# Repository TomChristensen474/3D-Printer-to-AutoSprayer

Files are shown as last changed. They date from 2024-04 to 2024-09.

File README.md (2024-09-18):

# 3D-Printer-to-AutoSprayer
## Introduction
This project is aimed at creating an affordable, accessible autosprayer by modifying your 3D printer. The process is non-destructive and you will retain the existing functionality of your 3D printer.

Taking it from a boring 3D printer to 3D Printer + AutoSprayer:

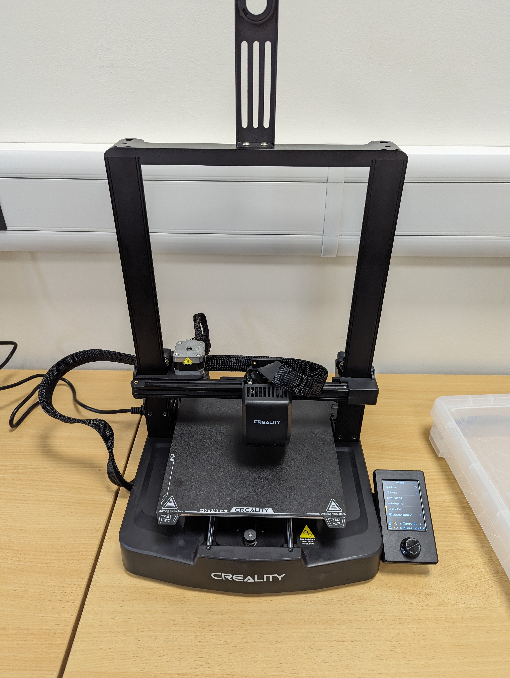
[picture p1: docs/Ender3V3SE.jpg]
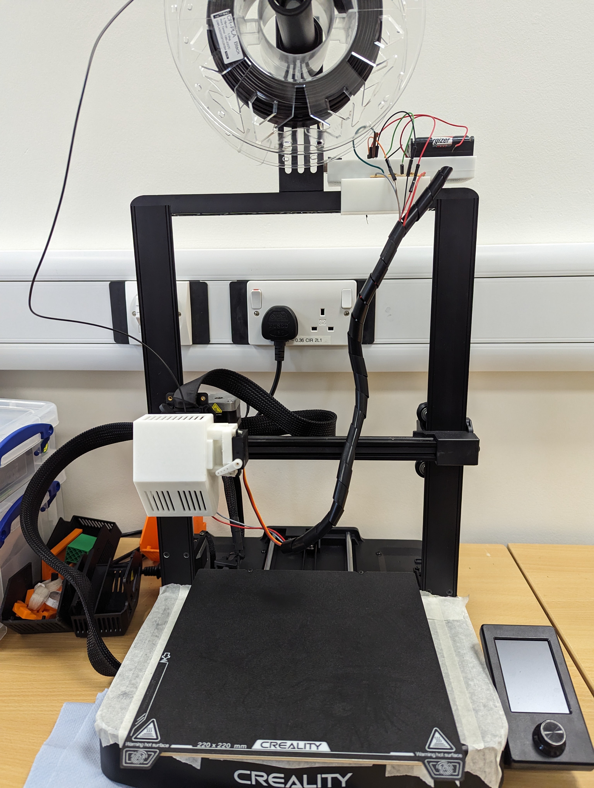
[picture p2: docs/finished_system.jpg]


https://github.com/user-attachments/assets/ce837ea1-1385-4ece-8191-b1b6b753dc1a

The video above shows a benchmark of the autosprayer's even spray-coating capabilities - apologies for Github's rotation of the portrait video.

This project was done using an Ender 3 V3 SE, the .stl files provided should therefore be adapted or replaced to suit your existing printer. But feel free to take inspiration from the designs. ;)

Speaking of inspiration: The idea for this project and some development was based off this original instructables article by user: Remi_Rafael so credit to them. <INSERT ORIGINAL INSTRUCTABLES>

## Quick-links
[System Requirements](#system-requirements)

[How does it work?](#how-does-it-work)

[How to set up](#how-to-set-up)

[Quick code breakdown](#the-code---what-does-it-do)

## System requirements
#### Expensive purchases :( 
* 3D printer
* Airbrush
* Compressor for airbrush
* Inks/Paints for airbrushing

#### Equipment you may already have on hand :)
* 2x Resistors in restistance ratio (<INSERT MY SPECIFIC ONES USED FOR ENDER 3 SYSTEM>)
* Arduino Uno (you can, of course, use whatever arduino you may have to hand, but the uno made it convenient with it's plethora of connections)
* 6xAA battery holder and (preferrably rechargeable) batteries (to power servo and circuit). If using an alternative method of powering the system, make sure it can handle the current draw of whatever servo you use. A simple USB will likely not be enough to power it.
* Servo motor (DS239-MG or equivalent) (<INSERT SPECIFIC ONE USED / SPECS>) 
* Heat-set threaded inserts and screws
* Cables
* Cable wrap for cable management

## How does it work?
#### Step 1 - Mounting the Airbrush
The airbrush is mounted onto the existing print-head using custom 3D printed models. To mount to the Ender 3 VS SE I used for the project, I chose to model a replacement print-head with a mount for the airbrush on the side. The .stl files for this printer are included.

#### Step 2 - Controlling Movement of the Print-Head/Airbrush
G-code is a widely used set of instructions used to control CNC machines and 3D printers. We can take advantage of G-code's existing functionality to do things like move the print head (and therefore the airbrush) to the position we desire. The instructions we take advantage of in this system can be found in the GCODE_writer class.

#### Step 3 - Controlling When/Where/What we Spray
We can take advantage of the parts-cooling fan in the printer in order to send a signal to our system telling us when, where and how much we want our airbrush to spray. This is a specific G-code instruction and sets our fan speeds between a range of 0 and 255, sending a different amount of voltage to the pins of the fan. By 'hijacking' this voltage and reading it using our arduino, we can send a signal to our servo motor telling it to turn a lot or a little, pulling the airbrush trigger back more or less respectively.

The circuit used for this is displayed below - both in schematic-form and in a simulator for the less electrically-inclined like myself.

## How to set up
You've got all the hardware, and you're ready to get spraying. How do you set all this up? (If you're using a CNC gantry or alternative printer to the Ender 3 V3 SE, there may be some additional trial and error with modeling and printing your own mounting hardware).
### Step 1 - Printing the mounting hardware
.stl files for the mounting hardware can be found in the models folder of this repository. First let's print the airbrush mount. There are 3 models to connect the airbrush to the print-head: a replacement print-head cover, an extended trigger to allow your servo to pull back the airbrush trigger, and a 'mate' to this print-head cover to hold the airbrush in place.

The models directory also contains a clip to mount your circuit to the frame of the Ender 3 V3 SE. A separate model is included which screws into the clip to hold an arduino uno and a battery. If you are using alternative hardware to an Arduino Uno, you can remodel this whilst still being able to use the clip provided. (The screw holes provided are M3).

I recommend test fitting all components now.

### Step 2 - Set up your circuit
I have provided a circuit schematic and diagram in the [section here](#step-3---controlling-whenwherewhat-we-spray).
For a picture of my assembled circuit, see below. My machine was only a prototype, so I didn't make any effort to permanently fix components in place. For longer-term use I would definitely recommend putting some effort into making it fit more compactly and robustly together (perhaps converting the circuit design into a PCB to make it more compact also).

It's important to note for the circuit to work that all ground connections must be linked (printer fan [next section], battery(/power supply), Arduino).

### Step 3 - Connect your circuit to your printer
To connect your circuit to the printer, we solder two leads from our circuit to the voltage and ground connections on the fan that is attached to the print-head.

If you are using a CNC 3D gantry or simply don't want to solder a connection to the fan on your printer. You can still use a button-controlled circuit to tell the circuit when to spray manually and achieve great results.

### Run the code
Load the relevant Arduino sketch onto your Arduino depending on if you're automated or button controlled spraying. You can then disconnect it if you wish as your battery/power supply can power the Arduino.

To run the ```spray_an_area.py``` script to generate ```.gcode``` to spray a desired area. You can run ```src/gcode_generation/spray_an_area.py``` with the following flags to specify the area you want to spray

```--start-position x y``` - sets the start position to `x` and `y`

```--spray-area w h``` - sets the dimensions of area to be sprayed to `w` (width) and `h` (height) in mm

```--destination filename``` - sets the destination filename of the .gcode file e.g. 'spray_an_area' -> `spray_an_area.gcode`

```--layers n``` - repeat for `n` layers

```--no-temp``` - do not set a target temperature or wait for temperature stabilisation

(```static_GCODE_script.py``` is also included, it takes no arguments and may be useful for debugging.)

### Step 5 - Testing
Now that your circuit is all connected, let's give it a test before we finish the assembly. Your printer's control software should have some way of manually turning on and off the fans on the print head like this on the Ender 3 V3 SE's menu (control->temperature->fans) pictured below.

When the fans are switched on you should see (and hear) your servo actuating to its 'spray' position. When the fans are switched off, you should see it return to its 'resting' position.

If you are using manually controlled spraying, add a button to your circuit and test that your servo activates when a button is pressed.

### Step 6 - Assembly and dry run
Your servo will be attached to the airbrush mounting hardware and will therefore have wires dangling down from the printer's frame. To tidy up these wires along with the leads connecting to the printer's fan, I highly suggest getting some cable wrap to route them all together and prevent unecessary strain on individual cables.

You can now load your airbrush onto your mounting hardware (without any ink loaded in the paint cup), with the extended trigger. Mount the servo as well and position the servo arm primed to push back the airbrush trigger.

Run the gcode_generation script ```spray_an_area.py``` with your desired spray area position and size. Load this onto your printer's SD card (or used networked printing options) and hit print.

You should see your print head strafe over your specified spray area and your servo should pull back the airbrush trigger at the start and end of each strafe.

You can use this opportunity to hone in your spraying dimensions.

### Step 7 - Mask your printer to protect from stray paint
Wait, wait, wait before you start spraying! Make sure you mask off your print bed, and the area around it to prevent getting paint on it.

If your printer has a magnetic print bed like the Ender 3 V3 SE, I would recommned getting a second one so you can hot-swap between spraying and printing more easily.

### Step 8 - Get creating!
You can create stencils using a laser or vinyl cutter (or masking) and now generate consistently sprayed images.
You could adapt my spraying code to spray patterns or images directly without requiring a stencil.
You can spray functional inks like I've done in my demo below to quickly generate functional prototypes on 3D printed objects.

If you do end up creating anything using this repo I'd love to see so please get in touch and show off what you've done!

## The Code - what does it do?
It can be a little overwhelming for some to dive into a repo and try and decipher what all the code does without a little extra explanation so I thought I'd provide that here:

There are two main components to the code provided. In the ```gcode_generation``` folder you will find code for a simple script to spray an even coat across a specific area as this was my goal for the project. (I used my 3D modeling software to create a mask on top of my print in the pattern for the circuit I wanted to make using sprayed functional inks). However the ```GCODE_writer``` class is provided and can be adapted or modified to spray more complex patterns or images. The ```spray_an_area.py``` python script contains arguments that are listed in the [relevant section](#run-the-code).

In the ```arduino_sketches``` folder you will find two very similar scripts with the purpose of controlling the activation of a servo. ```automatic_spray.py``` is an example script that controls the spraying automatically from aforementioned G-code instructions for turning the fan on-and-off. ```button_spray.py``` is an alternative example where spraying can be manually controlled by button-press in the event that alternative printers do not provide as easy access to fan control as with the Ender 3 VS SE (I assume most will as print-heads must be cooled somehow).

Lastly (for my research purposes) there is an evaluation script (```evaluation.py```) provided. This was used for evaluating the performance of the system with regards to applying an even coat of acrylic paint across an paper by seeing how much light passed through - which is important for my application of spraying functional inks to create circuits. You can very likely ignore this but I thought I would include it nonetheless.

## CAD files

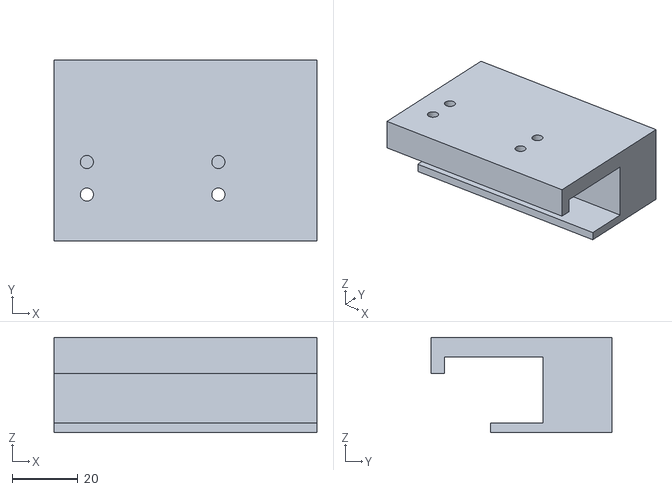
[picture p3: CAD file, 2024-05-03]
models/Ender_3_Clip v16.stl
80.0 x 55.0 x 29.0

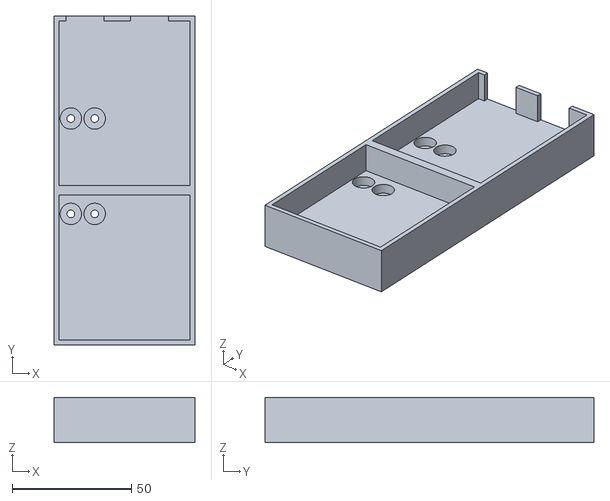
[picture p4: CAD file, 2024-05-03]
models/Ender_3_Uno_Mount v16.stl
59.0 x 138.0 x 19.0

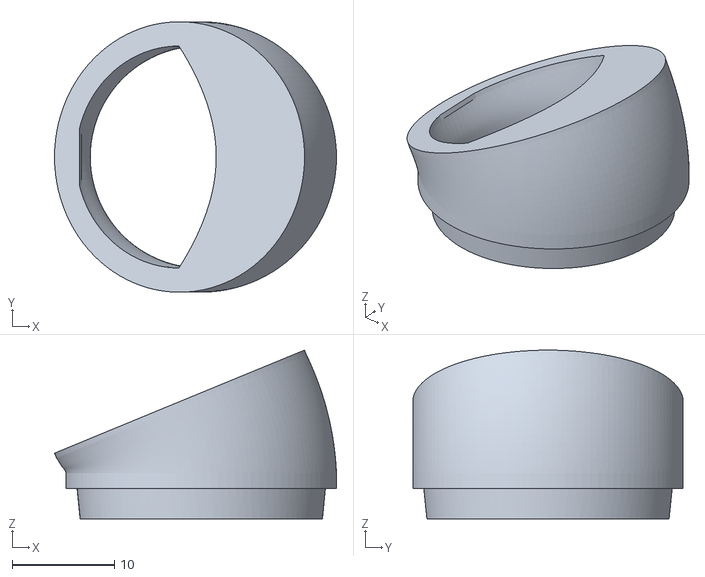
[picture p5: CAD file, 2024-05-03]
models/Airbrush cap v1.stl
27.6 x 26.5 x 16.5

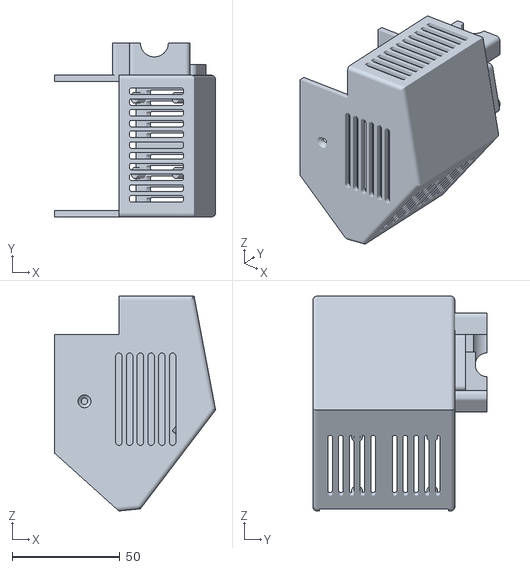
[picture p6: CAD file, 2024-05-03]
models/3D_printer_cover_print_head v22.stl
75.0 x 81.0 x 100.0

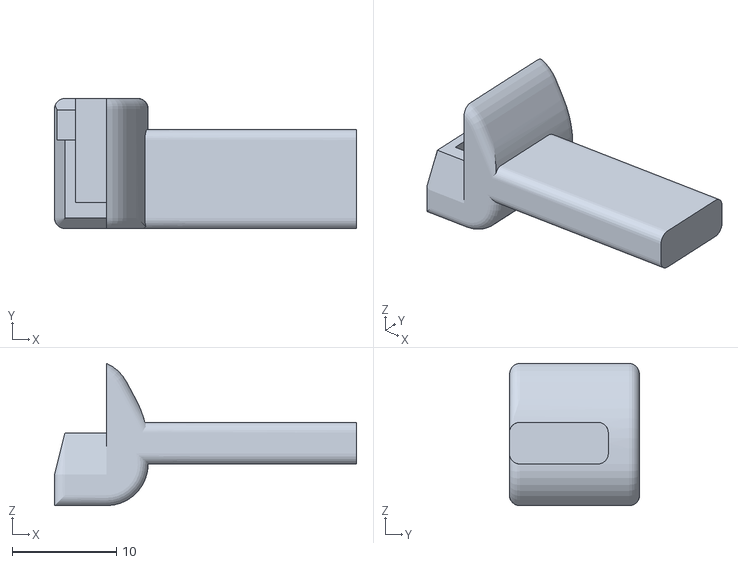
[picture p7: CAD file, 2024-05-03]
models/3D_printer_cover v22.stl
29.0 x 12.5 x 13.7

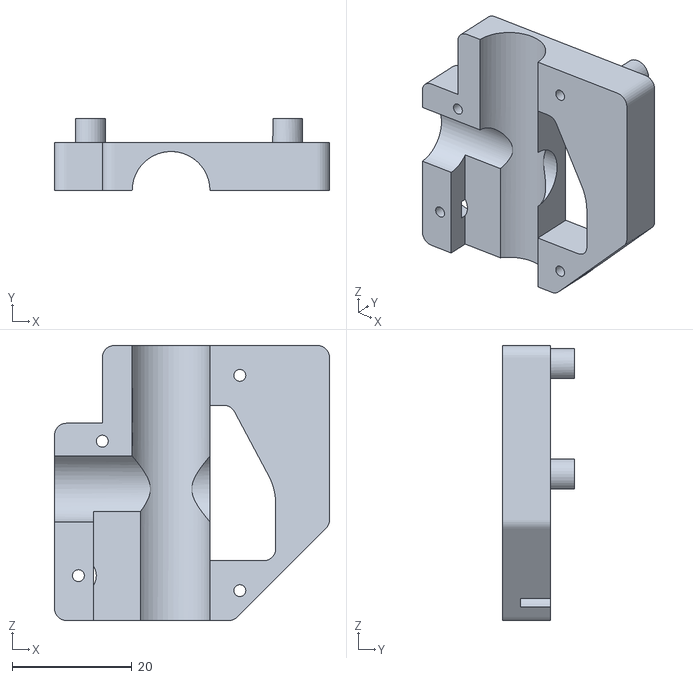
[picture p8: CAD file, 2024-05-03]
models/3D_printer_cover_mate v22.stl
46.0 x 12.0 x 46.0

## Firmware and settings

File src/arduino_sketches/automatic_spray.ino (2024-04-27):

#include <Servo.h>

Servo servo;

int voltage_input_pin = A0;
int servo_pin = 9;
int no_spray_angle = 10;
int spray_angle = 65;
int angle;

void setup()
{
  Serial.begin(9600);

  servo.attach(servo_pin);

  pinMode(voltage_input_pin, INPUT);
  pinMode(LED_BUILTIN, OUTPUT);

  angle = no_spray_angle;
  servo.write(angle);
}

void loop()
{
  int sensor_value = analogRead(A0);
  float voltage = sensor_value * (5.0 / 1023.0);
  if (voltage > 1)
  {
    digitalWrite(LED_BUILTIN, HIGH);

    if (angle <= spray_angle)
    {
      angle++;
      delay(3);
    }
  }
  else
  {
    digitalWrite(LED_BUILTIN, LOW);

    if (angle > no_spray_angle)
    {
      angle--;
      delay(3);
    }
  }

  servo.write(angle);
}

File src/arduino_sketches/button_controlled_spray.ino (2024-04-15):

#include <Servo.h>

Servo servo;

int button_pin = 12;
int servo_pin = 9;
int no_spray_angle = 0;
int spray_angle = 90;
int angle;

void setup()
{
  Serial.begin(9600);

  servo.attach(servo_pin);

  pinMode(button_pin, INPUT_PULLUP);
  pinMode(LED_BUILTIN, OUTPUT);

  angle = no_spray_angle;
  servo.write(angle);
}

void loop()
{
  // Serial.println(digitalRead(button_pin));
  if (digitalRead(button_pin) == LOW)
  {
    digitalWrite(LED_BUILTIN, HIGH);

    if (angle <= spray_angle)
    {
      angle++;
      delay(2);
    }
  }
  else
  {
    digitalWrite(LED_BUILTIN, LOW);

    if (angle > no_spray_angle)
    {
      angle--;
      delay(2);
    }
  }

  servo.write(angle);
}

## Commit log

2024-04-07 adding initial arduino sketches
2024-04-07 updating arduino sketches - demo still incomplete
2024-04-15 updating script to take advantage of fan
2024-04-27 adding cropped test images and updating test script
    [results.csv]
2024-04-27 arduino script now uses analog voltage and a different spray angle
2024-05-03 deleting results.csv and making capacitive_touch_demo_work
    [results.csv]
2024-05-03 adding models to GH
    [3D_printer_cover v22.stl, 3D_printer_cover_mate v22.stl, 3D_printer_cover_print_head v22.stl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]
